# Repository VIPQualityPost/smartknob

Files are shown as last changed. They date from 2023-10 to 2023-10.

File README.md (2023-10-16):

# SmartKnob
SmartKnob is an open-source input device with software-configurable endstops and virtual detents.

A brushless gimbal motor is paired with a magnetic encoder to provide closed-loop torque feedback control, making it
possible to dynamically create and adjust the feel of detents and endstops.

Join the [Discord community](https://discord.gg/5jyhjcbTnR) to discuss the project with others, show off your build, or help answer each others' questions!




# Designs

## SmartKnob View
The "SmartKnob View" is the premium SmartKnob experience with an integrated display shown in my [demo video](https://www.youtube.com/watch?v=ip641WmY4pA). Under active development.

🎉 **Motors are [now available](https://www.sparkfun.com/products/20441)!** If you've been following this project,
you'll know that the recommended motors went out of stock nearly immediately after it was published.
Thanks to [the community](https://github.com/scottbez1/smartknob/issues/16#issuecomment-1094482805%5D), we were able to
identify the likely original manufacturer, and recently SparkFun Electronics has been getting them produced and regularly
[stocking them](https://www.sparkfun.com/products/20441)! (However, they've been selling out quickly each time they restock, so definitely sign up for backorder notifications if they're out of stock when you check). Thanks to everyone who helped search and investigate different
motor options along the way!

Features:
 - 240x240 round LCD ("GC9A01"), protected by 39.5mm watch glass on rotor
 - BLDC gimbal motor, with a hollow shaft for mechanically & electrically connecting the LCD
 - Powered by ESP32-PICO-V3-02 (Lilygo TMicro32 Plus module)
 - PCB flexure and SMD resistors used as strain gauges for press detection (haptic feedback provided via the motor)
 - 8 side-firing RGB LEDs (SK6812-SIDE-A) illuminate ring around the knob
 - USB-C (2.0) connector for 5V power and serial data/programming (CH340)
 - VEML7700 ambient light sensor for automatic backlight & LED intensity adjustment
 - Versatile back plate for mounting - use either 4x screws, or 2x 3M medium Command strips (with cutouts for accessing removal tabs after installation)
 - Front cover snaps on for easy access to the PCB

**Current status:** Not recommended for general use, but may be a fun project for an advanced electronics hobbyist.

### Demo video

<a href="https://www.youtube.com/watch?v=ip641WmY4pA">
    
</a>

### How it works
<a href="https://www.youtube.com/watch?v=Q76dMggUH1M">
    
</a>

### 3D CAD

Exploded view

Latest Fusion 360 Model: https://a360.co/3BzkU0n

### Build your own?

While this is a "DIY" open-source project, it is not yet a mature plug-and-play project. If you intend to build your own, note that it requires advanced soldering experience to build - very small-pitch surface-mount soldering is required (reflow or hot air recommended), and assembly is quite time-consuming and delicate. Please go into it with the expectation that you will almost certainly need to be able to troubleshoot some hardware and firmware issues yourself - I recommend reviewing/understanding the schematics and basic firmware before jumping in!

More documentation on the BOM and what parts you need to order is coming in the future - thanks so much for your interest! Follow me on [Twitter](https://twitter.com/scottbez1) for the latest updates on this and other projects.

View the latest auto-generated (untested) [Base PCB Interactive BOM](https://smartknob-artifacts.s3.us-west-1.amazonaws.com/master/electronics/view_base-ibom.html) and [Screen PCB Interactive BOM](https://smartknob-artifacts.s3.us-west-1.amazonaws.com/master/electronics/view_screen-ibom.html) (or, the combined [BOM csv](https://smartknob-artifacts.s3.us-west-1.amazonaws.com/master/electronics/view_base-bom.csv)) for electronics/hardware parts list. ⚠️ These are auto-generated from the latest untested revision on GitHub. For tested/stable/recommended artifacts, use a [release](https://github.com/scottbez1/smartknob/releases) instead.

A few miscellaneous notes in the meantime:

 - There's limited space inside the LCD mount for wiring, and 8 wires need to fit through the hole in the center. I used 30 AWG wire-wrapping wire. Enamel-coated wire would probably work too.
 - Older versions of the design (as seen in the videos) used glued-on BF350-3AA strain gauges to detect presses; in v0.5 these were replaced with footprints for SMD resistors, which exhibit similar properties when stretched/compressed and are much easier to assemble. 
 - The TMC6300 is _tiny_ and has a bottom pad, so I would seriously consider getting a stencil along with the PCB order. Even with the stencil I needed to manually clean up some bridging afterward; I _highly_ recommend Chip Quik NC191 gel flux, available on [Amazon](https://amzn.to/3MGDSr5) (or use this [non-affiliate link](https://www.amazon.com/Smooth-Flow-No-Clean-syringe-plunger/dp/B08KJPG3NZ) instead) or from your electronics distributor of choice. Flux is also very helpful when soldering the LCD ribbon cable to to screen PCB.
 - For breadboard prototyping, the [TMC6300-BOB](https://www.trinamic.com/support/eval-kits/details/tmc6300-bob/) or SparkFun's [TMC6300 driver board](https://www.sparkfun.com/products/21867) are awesome and way easier to work with than the bare chip if you just want to play around with low current BLDC motors
 - For AliExpress purchases: I highly recommend **only** using AliExpress Standard Shipping (purchasing in the US). I have had multiple purchases take months or never get delivered when purchased with Cainiao or other low cost shipping options, whereas AliExpress Standard is very reliable and generally faster in my experience.
 - Make sure to check the [open issues](https://github.com/scottbez1/smartknob/issues) - this design is not yet "stable", so beware that everything may not go smoothly.

Future plans:
 - consider switch to using an ESP32-S3-MINI-1 module
 - get wifi configured and working (probably MQTT?). Currently memory is an issue with the full display framebuffer sprite. PSRAM might fix this (requires newer ESP-IDF & unreleased Arduino core, and from a brief test I got horrible performance with PSRAM enabled), or the next item might help reduce memory:
 - migrate to LVGL, for better display rendering and easy support for menus, etc. Shouldn't require a full 240x240x24b framebuffer in memory, freeing some for wifi, etc.
 - Home Assistant integration, or other real-world applications
 - ???
 - [Profit](https://github.com/sponsors/scottbez1/) 😉

 #### Already built one?
Check out the [firmware/software documentation](https://paper.dropbox.com/doc/SmartKnob-firmware-and-software--B_oWj~L1dXqHgAqqYmhwwuqzAg-VUb9nq7btuhnHw5KlgJIH)
for tips on getting it programmed and hooking it up to your own software integrations.

If you've already uploaded the standard firmware and gone through the calibration process (see guide linked above if you don't know what this means),
go to https://scottbez1.github.io/smartknob/ to try out an interactive web-based demo that uses Web Serial to talk to a SmartKnob that's plugged into your
computer's USB port!

#### Base PCB

<a href="https://smartknob-artifacts.s3.us-west-1.amazonaws.com/master/electronics/view_base-front-3d.png">
    
</a>
<a href="https://smartknob-artifacts.s3.us-west-1.amazonaws.com/master/electronics/view_base-back-3d.png">
    
</a>

Ordering notes: use white soldermask, for reflecting light from RGB LED ring around the knob. Should be 1.2mm thick (not "standard" 1.6mm).

If you are ordering a stencil for solder paste from JLCPCB and plan to apply paste by hand (as
[shown in the video](https://youtu.be/Q76dMggUH1M?t=372)) without a stencil frame/machine, make sure to select
**"Customized size"** and enter smaller dimensions (e.g. 100mm x 100mm) to avoid getting a much larger stencil than you
need. This will also likely reduce the cost of shipping substantially! Also, select only the **Top** side; the bottom
only has 2 SMT components - the motor connector and VEML7700 ALS - so it's not worth getting a stencil for that.

Latest auto-generated (untested and likely broken!) artifacts⚠️:

[Schematic](https://smartknob-artifacts.s3.us-west-1.amazonaws.com/master/electronics/view_base-schematic.pdf)

[Interactive BOM](https://smartknob-artifacts.s3.us-west-1.amazonaws.com/master/electronics/view_base-ibom.html)

[PCB Packet](https://smartknob-artifacts.s3.us-west-1.amazonaws.com/master/electronics/view_base-pcb-packet.pdf)

[Gerbers](https://smartknob-artifacts.s3.us-west-1.amazonaws.com/master/electronics/view_base-jlc/gerbers.zip)

⚠️ For tested/stable/recommended artifacts, use a [release](https://github.com/scottbez1/smartknob/releases) instead.

#### Screen PCB

<a href="https://smartknob-artifacts.s3.us-west-1.amazonaws.com/master/electronics/view_screen-front-3d.png">
    
</a>
<a href="https://smartknob-artifacts.s3.us-west-1.amazonaws.com/master/electronics/view_screen-back-3d.png">
    
</a>

Ordering notes: Must be 1.2mm thick (not "standard" 1.6mm) per mechanical design. (The PCB silkscreen mentions 0.6mm thickness - this is the thickness of the **VHB tape** for adhering the LCD; the PCB should be 1.2mm thick)

There are few enough components on the Screen PCB that I chose to hand-solder them rather than reflow with solder paste
and a stencil, but if you order a stencil, see the note above about selecting a "Customized size" to be easier to
handle and save on shipping. Also make sure to select the **Bottom** side only; all the components are on the bottom
side of the screen PCB.

Latest auto-generated (untested and likely broken!) artifacts⚠️:

[Schematic](https://smartknob-artifacts.s3.us-west-1.amazonaws.com/master/electronics/view_screen-schematic.pdf)

[Interactive BOM](https://smartknob-artifacts.s3.us-west-1.amazonaws.com/master/electronics/view_screen-ibom.html)

[PCB Packet](https://smartknob-artifacts.s3.us-west-1.amazonaws.com/master/electronics/view_screen-pcb-packet.pdf)

[Gerbers](https://smartknob-artifacts.s3.us-west-1.amazonaws.com/master/electronics/view_screen-jlc/gerbers.zip)

⚠️ For tested/stable/recommended artifacts, use a [release](https://github.com/scottbez1/smartknob/releases) instead.

#### Printed parts
You will need six printed parts. The current stable designs can be found as STL assets in the [v185 mechanical release](https://github.com/scottbez1/smartknob/releases/tag/releases%2Fmechanical%2Fv185-dummy-tag) or you can export the latest untested designs from the CAD model by opening it in Fusion 360: https://a360.co/3BzkU0n

The parts can _probably_ be FDM 3D printed with a well-tuned printer, but the parts shown in videos/photos were MJF printed in nylon for tight tolerances and better surface finish. 

If you wanted a simpler build, you could omit the LCD and just merge the knob + glass from the model into a single STL to get a closed-top knob.

Export and print the following 6 parts:
* `Enclosure`
* `Knob` (RotorAssembly->KnobAssembly->Knob)
* `ScreenPlatform`
* `RotorSpacer` (RotorAssembly->RotorSpacer)
* `MountBase`
* `BackPlate`

⚠️ If you opt to go for MJF Nylon printing from JLCPCB, their system may complain about `< 0.8mm wall thickness detected` on the `MountBase`, `ScreenPlatform` and `RotorSpacer` parts. This appears to be a false positive, possibly on some of the print tapers. You should be able to ignore this, as all print orders at JLCPCB are subject to a final manual review, and they will contact you by email if there are any job-stopping issues or risks with your prints.

## NanoFOC (3rd party)
If you're looking to tinker with FOC/haptic feedback, but don't want to build a full SmartKnob View yourself, I can
recommend the NanoFOC DevKit++, an [open-source design](https://github.com/katbinaris/nanofoc_devkit) made and
[sold](https://store.binaris.io/products/nanofoc-devkit) by a member of the SmartKnob community! It's super compact
and is a great testbed or core for building your own BLDC-based haptic input device.

Image of the NanoFOC PCB

The NanoFOC uses an ESP32-S3, and the SmartKnob firmware works on it out of the box; just select the `nanofoc`
environment in PlatformIO rather than the `view` environment when uploading.

# Frequently Asked Questions (FAQ)

### Can I use this cheap gimbal BLDC motor I found on AliExpress?

I can't stop you, but I will caution that **you probably won't be super happy with it** depending on your intended application.

Nearly every off-the-shelf BLDC gimbal motor that the community has tested (which is pretty much ALL the cheap ones you'll find on AliExpress, trust me) has
_moderate to severge cogging_. That means the motor wants to snap to certain positions by itself even when unpowered. This means you won't be able to get
completely smooth rotation when virtual detents are turned off, and the motor's cogging may interfere with or overpower the virtual detents, particularly if
you set them to lower strength or make then very fine-grained.

The recommended motor is definitely the best (i.e. lowest cogging) off-the-shelf motor we've come across so far, and is the only readily-available motor
that I would consider "good" for this application.

If you've found another motor that is completely smooth when unpowered, we'd LOVE to hear about it in the discord; if you're wondering about some cheap motor
you saw online, either just order one and try it for yourself, or ask about it in discord but don't be surprised (or offended) if the response you get is
something terse like "nope, no good".

### How much does it cost?

I wish I could tell you now, but I don't actually know off the top of my head. Check back soon - I've only built a few so far, which was the result of a bunch of tinkering and prototyping over an extended period, so I don't have all the expenses tallied up yet. Probably less than $200 in parts? But some items have gotten more expensive, and you may be limited by minimum order quantities or shipping charges from multiple separate suppliers.

### Does it work with XYZ?

Not yet, regardless of whatever "XYZ" you're thinking of. So far I've only implemented enough firmware for the demo shown in the video, so you can't actually use it for anything productive yet. The basic detent configuration API is there, but not much else. Lots of firmware work remains to be done. If you build one, I'd love your help adding support for "XYZ" though!

### Can I buy one as a kit or already assembled?

Probably not? Or at least, I don't have any immediate plans to sell them myself. It's not that I don't want you to be happy, but hardware is a hard business and I just work on this stuff in my free time.

It's open source with a fairly permissive license though, so in theory anyone could start offering kits/assemblies. If someone does go down that route of selling them, note that attribution is
 _required_ (and I wouldn't say no to [royalties/tips/thanks](https://github.com/sponsors/scottbez1/) if you're in a giving mood 🙂).

# Firmware and Software
More extensive documentation of the firmware and software (and how to get started) can be found in the dedicated [SmartKnob Firmware and Software Guide](https://paper.dropbox.com/doc/SmartKnob-firmware-and-software--Byho6npe9XvZLZLxJ_8bK5TqAg-VUb9nq7btuhnHw5KlgJIH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)

## General Component Info

### Magnetic encoders

#### MT6701 (MagnTek)
Excellent sensor at a reasonable price - highly recommended. Less noisy than TLV493D, and more responsive (control loop is more stable) using SSI.

 - Lots of IO options - SSI, I2C, and ABZ - should offer good response latency
 - SSI includes CRC to validate data
 - No power-down or low-power options - may not be ideal for battery-powered devices
 - Not available from US distributors (Mouser, Digi-Key)

[Datasheet](http://www.magntek.com.cn/upload/MT6701_Rev.1.5.pdf)

[Ordering (LCSC)](https://lcsc.com/product-detail/Angle-Linear-Position-Sensors_Magn-Tek-MT6701CT-STD_C2856764.html)

#### TLV493D (Infineon)
Not used in the SmartKnob view, but a common/popular magnetic encoder in general. It's a mediocre choice for a haptic feedback implementation. Easy to prototype with using [Adafruit's QWIIC breakout board](https://www.adafruit.com/product/4366).

In my testing, it's noisy, requiring filtering/smoothing that can slow responsiveness, hurting control loop stability. Or, with less filtering, the noise
can easily be "amplified" by the derivative component in the PID motor torque controller, causing audible (and tactile) humming/buzzing.

But the bigger issue is that there is apparently a known silicon issue that causes the internal ADC to sometimes completely lock up, requiring a full reset and re-configuration, which can cause delays/gaps in data! See section
5.6 in the [User Manual](https://www.infineon.com/dgdl/Infineon-TLV493D-A1B6_3DMagnetic-UM-v01_03-EN.pdf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)

    In the Master Controlled Mode (MCM) or the Fast Mode (FM) the ADC conversion may hang up. A hang up can
    be detected by:
     - Frame Counter (FRM) counter stucks and does not increment anymore.

In my experience testing 4 different Adafruit breakout boards, 2 of them (50%) regularly exhibit this lockup behavior within a minute or two of use. It is possible to detect and auto-reset (and there is code in the project to do so), but it is slow and may cause undesirable jumps/delays if the sensor locks up often.

[Datasheet](https://www.mouser.com/datasheet/2/196/Infineon_TLV493D_A1B6_DataSheet_v01_10_EN-1227967.pdf)

#### AS5600 (AMS)
A mediocre choice. Cheap breakout boards are readily available.

In my testing, it's fairly noisy (anecdotally, noisier than the TLV493d), requiring filtering/smoothing that can slow responsiveness, hurting control loop stability. Additionally, it saturates at a lower magnetic field strength than other sensors I tested, requiring a significant air gap (8-10mm) when used with a strong neodymium diametric magnet like [Radial Magnets 8995](https://www.digikey.com/en/products/detail/radial-magnets-inc/8995/5126077).

[Datasheet](https://ams.com/documents/20143/36005/AS5600_DS000365_5-00.pdf)

### Motor drivers
#### TMC6300-LA
This is a relatively new IC and it's a perfect match! There generally aren't any other drivers (with integrated fets) that meet the requirements for the low-voltage and low-current motors used in this project (DRV8316 might work, but has not been tested).

Highlights:
 - 2-11V DC motor supply input
 - Up to 1.2A RMS
 - Tiny (3x3mm QFN)

 [Datasheet](https://www.trinamic.com/fileadmin/assets/Products/ICs_Documents/TMC6300_datasheet_rev1.07.pdf)

 [Product page](https://www.trinamic.com/products/integrated-circuits/details/tmc6300-la/)

### Motors
#### 32mm Rotor, Hollow Shaft, Diametric magnet



- 32mm rotor
- 15mm overall height (including magnet), 12.75mm height w/o magnet, 9mm rotor height
- low/zero cogging - excellent for completely smooth input
- 5.9mm hollow shaft
- built-in diametric magnet for encoder
- Proven option

This is overall the easiest motor to get started with. Low cogging and a built-in diametric magnet are great!

Available [from SparkFun](https://www.sparkfun.com/products/20441)!

# Acknowledgements
This project was greatly inspired by Jesse Schoch's video "[haptic textures and virtual detents](https://www.youtube.com/watch?v=1gPQfDkX3BU)" and the
corresponding [discussion in the SimpleFOC community](https://community.simplefoc.com/t/haptic-textures/301). Seriously, this project wouldn't exist if not for that video - thank you Jesse!

# License

This project is licensed under Apache v2 (software, electronics, documentation) and Creative Commons Attribution 4.0 (hardware/mechanical) (see [LICENSE.txt](LICENSE.txt) and [Creative Commons](https://creativecommons.org/licenses/by/4.0/)).

    Copyright 2022 Scott Bezek
    
    Licensed under the Apache License, Version 2.0 (the "License");
    you may not use this file except in compliance with the License.
    You may obtain a copy of the License at
    
        http://www.apache.org/licenses/LICENSE-2.0
    
    Unless required by applicable law or agreed to in writing, software
    distributed under the License is distributed on an "AS IS" BASIS,
    WITHOUT WARRANTIES OR CONDITIONS OF ANY KIND, either express or implied.
    See the License for the specific language governing permissions and
    limitations under the License.

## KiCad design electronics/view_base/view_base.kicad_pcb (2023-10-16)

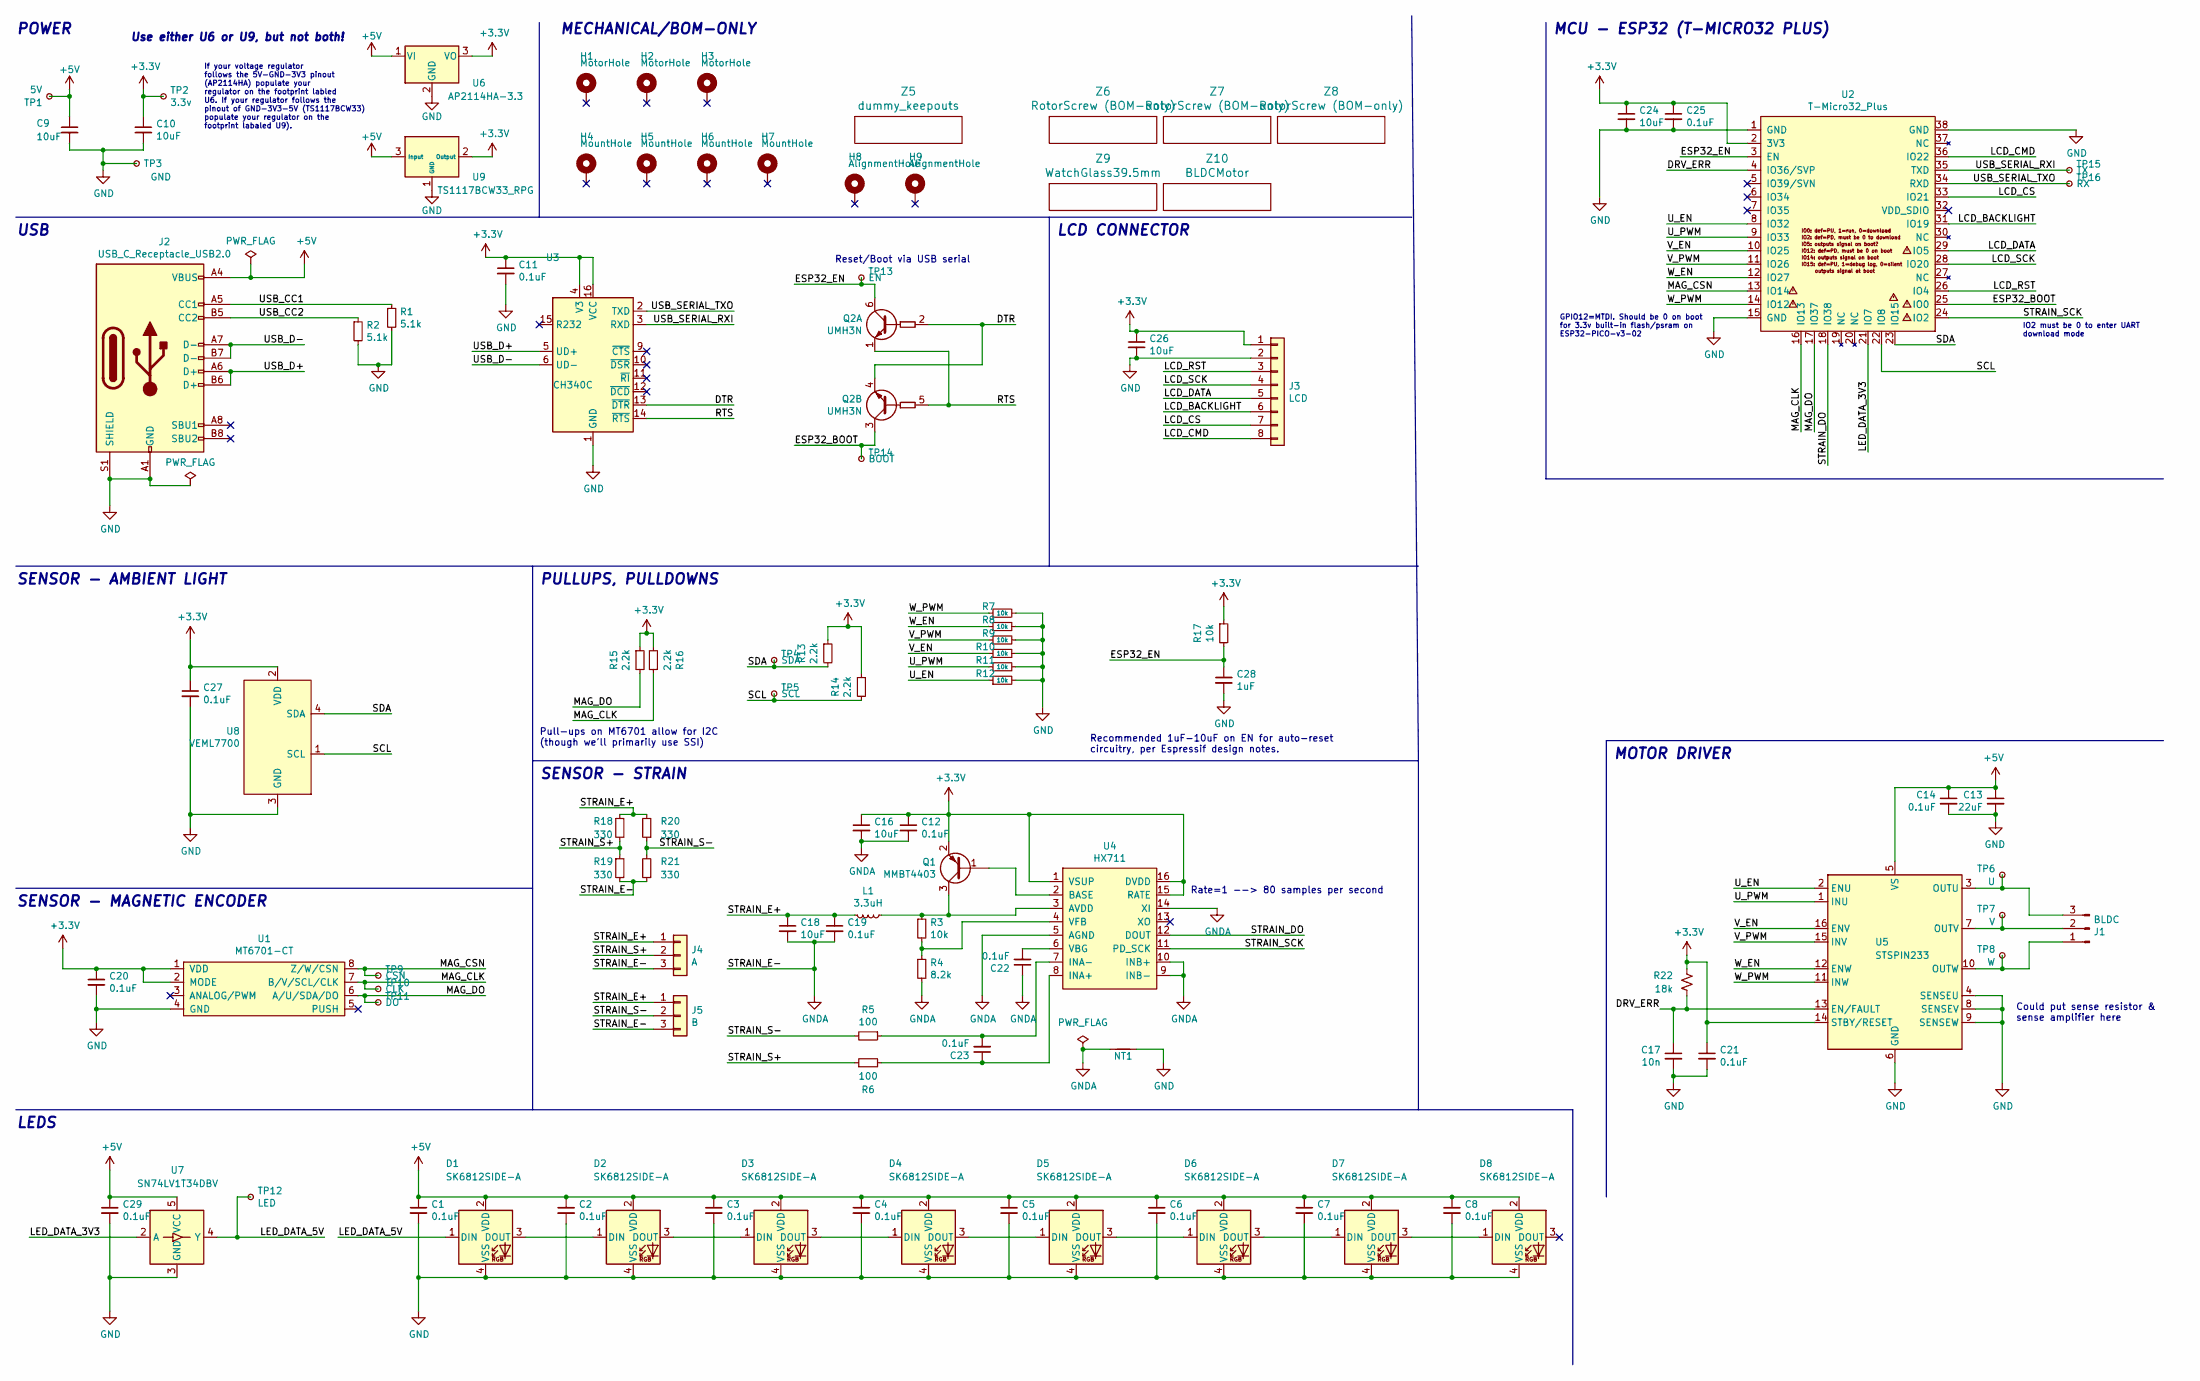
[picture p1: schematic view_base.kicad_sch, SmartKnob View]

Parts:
C1, C2, C3, C4, C5, C6, C7, C8, C11, C12, C14, C19, C20, C21, C22, C23, C25, C27, C29: 0.1uF; C_0603_1608Metric; LCSC C1591
C9, C10, C16, C18, C24, C26: 10uF; C_0805_2012Metric; LCSC C2922480
C13: 22uF; C_0805_2012Metric; LCSC C98190
C17: 10n; C_0603_1608Metric; LCSC C1591
C28: 1uF; C_0603_1608Metric; Mouser 187-CL10A105KA8NNNC
D1, D2, D3, D4, D5, D6, D7, D8: SK6812SIDE-A; SK6812-SIDE-A; Digikey 1528-4691-ND
H1, H2, H3: MotorHole; MountingHole_M1.6; LCSC C2931389
H4, H5, H6, H7: MountHole; MountingHole_2.2mm_M2_ISO7380_Pad_NonVirtual; LCSC C2911210 or C2911532 (screw), C2961595 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
H8, H9: AlignmentHole; MountingHole_2.2mm_M2_ISO7380_Pad_NonVirtual
J1: BLDC; 532610371; LCSC C293630
J2: USB_C_Receptacle_USB2.0; USB4510_NoPaste; LCSC C428463
J3: LCD; SolderPads_2mm_8
J4: A; SolderPads_2mm_3_STRAIN
J5: B; SolderPads_2mm_3_STRAIN
L1: 3.3uH; L_0805_2012Metric; LCSC C307744
NT1: NetTie_2; NetTie-2_SMD_Pad0.5mm
Q1: MMBT4403; SOT-23; LCSC C78864
Q2: UMH3N; SOT-363_SC-70-6; LCSC C62892
R1, R2: 5.1k; R_0603_1608Metric; LCSC C105580
R3, R7, R8, R9, R10, R11, R12, R17: 10k; R_0603_1608Metric; LCSC C98220
R4: 8.2k; R_0603_1608Metric; LCSC C114637
R5, R6: 100; R_0603_1608Metric; LCSC C319953
R13, R14, R15, R16: 2.2k; R_0603_1608Metric; LCSC C4190
R18, R19, R20, R21: 330; R_2512_6332Metric; LCSC C19866
R22: 18k; R_0603_1608Metric
TP1: 5V; TestPoint_Pad_D2.0mm_ValueSilk
TP2: 3.3v; TestPoint_Pad_D2.0mm_ValueSilk
TP3: GND; TestPoint_Pad_D2.0mm_ValueSilk
TP4: SDA; TestPoint_Pad_D2.0mm_ValueSilk
TP5: SCL; TestPoint_Pad_D2.0mm_ValueSilk
TP6: U; TestPoint_Pad_D2.0mm_ValueSilk
TP7: V; TestPoint_Pad_D2.0mm_ValueSilk
TP8: W; TestPoint_Pad_D2.0mm_ValueSilk
TP9: CSN; TestPoint_Pad_D2.0mm_ValueSilk
TP10: CLK; TestPoint_Pad_D2.0mm_ValueSilk
TP11: DO; TestPoint_Pad_D2.0mm_ValueSilk
TP12: LED; TestPoint_Pad_D2.0mm_ValueSilk
TP13: EN; TestPoint_Pad_D2.0mm_ValueSilk
TP14: BOOT; TestPoint_Pad_D2.0mm_ValueSilk
TP15: TX; TestPoint_Pad_D2.0mm_ValueSilk
TP16: RX; TestPoint_Pad_D2.0mm_ValueSilk
U1: MT6701-CT; SOIC-8_3.9x4.9mm_P1.27mm; LCSC C2856764, or C3003196
U2: T-Micro32_Plus; T-Micro32; Digikey N/A
U3: CH340C; SOIC-16_3.9x9.9mm_P1.27mm; LCSC C84681
U4: HX711; SOIC-16_3.9x9.9mm_P1.27mm; LCSC C43656
U5: STSPIN233; VQFN-16-1EP_3x3mm_P0.5mm_EP1.8x1.8mm
U6: AP2114HA-3.3; SOT-223-3_TabPin2_InGndOut; LCSC C460314
U7: SN74LV1T34DBV; SOT-23-5; LCSC C100024
U8: VEML7700; VEML7700-TOP; Digikey VEML7700-TT
U9: TS1117BCW33_RPG; SOT-223-3_TabPin2_GndOutIn; LCSC C6186, C35879, or others
Z5: dummy_keepouts; ViewKeepouts3d
Z6, Z7, Z8: RotorScrew (BOM-only); bom_only_no_pin
Z9: WatchGlass39.5mm; bom_only_no_pin
Z10: BLDCMotor; bom_only_no_pin

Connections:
+3V3: C10.1, C11.1, C12.1, C16.1, C20.1, C21.1, C24.1, C25.1, C26.1, C27.1, J3.1, Q1.2 (E), R13.1, R14.1, R15.1, R16.2, R17.1, R22.1, TP2.1, U1.1 (VDD), U1.2 (MODE), U2.2 (3V3), U3.4 (V3), U3.16 (VCC), U4.1 (VSUP), U4.15 (RATE), U4.16 (DVDD), U5.14 (STBY/RESET), U6.3 (VO), U8.2 (VDD), U9.2 (Output)
+5V: C1.1, C2.1, C3.1, C4.1, C5.1, C6.1, C7.1, C8.1, C9.1, C13.1, C14.1, C29.1, D1.2 (VDD), D2.2 (VDD), D3.2 (VDD), D4.2 (VDD), D5.2 (VDD), D6.2 (VDD), D7.2 (VDD), D8.2 (VDD), J2.A4 (VBUS), J2.A9 (VBUS), J2.B4 (VBUS), J2.B9 (VBUS), TP1.1, U5.5 (VS), U6.1 (VI), U7.5 (VCC), U9.3 (Input)
/DRV_ERR: C17.1, R22.2, U2.4 (IO36/SVP), U5.13 (EN/FAULT)
/DTR: Q2.2 (B1), Q2.4 (E2), U3.13 (~DTR)
/ESP32_BOOT: Q2.3 (C2), TP14.1, U2.25 (IO0)
/ESP32_EN: C28.1, Q2.6 (C1), R17.2, TP13.1, U2.3 (EN)
/LCD_BACKLIGHT: J3.6, U2.31 (IO19)
/LCD_CMD: J3.8, U2.36 (IO22)
/LCD_CS: J3.7, U2.33 (IO21)
/LCD_DATA: J3.5, U2.29 (IO5)
/LCD_RST: J3.3, U2.26 (IO4)
/LCD_SCK: J3.4, U2.28 (IO20)
/LED_DATA_3V3: U2.21 (IO7), U7.2 (A)
/LED_DATA_5V: D1.1 (DIN), TP12.1, U7.4 (Y)
/MAG_CLK: R16.1, TP10.1, U1.7 (B/V/SCL/CLK), U2.16 (IO13)
/MAG_CSN: TP9.1, U1.8 (Z/W/CSN), U2.13 (IO14)
/MAG_DO: R15.2, TP11.1, U1.6 (A/U/SDA/DO), U2.17 (IO37)
/RTS: Q2.1 (E1), Q2.5 (B2), U3.14 (~RTS)
/SCL: R14.2, TP5.1, U2.22 (IO8), U8.1 (SCL)
/SDA: R13.2, TP4.1, U2.23 (IO15), U8.4 (SDA)
/STRAIN_DO: U2.18 (IO38), U4.12 (DOUT)
/STRAIN_E+: C18.1, C19.1, J4.1, J5.1, L1.2, R18.1, R20.2
/STRAIN_S+: J4.2, R6.1, R18.2, R19.1
/STRAIN_S-: J5.2, R5.2, R20.1, R21.2
/STRAIN_SCK: U2.24 (IO2), U4.11 (PD_SCK)
/USB_CC1: J2.A5 (CC1), R1.1
/USB_CC2: J2.B5 (CC2), R2.1
/USB_D+: J2.A6 (D+), J2.B6 (D+), U3.5 (UD+)
/USB_D-: J2.A7 (D-), J2.B7 (D-), U3.6 (UD-)
/USB_SERIAL_RXI: TP15.1, U2.35 (TXD), U3.3 (RXD)
/USB_SERIAL_TXO: TP16.1, U2.34 (RXD), U3.2 (TXD)
/U_EN: R12.1, U2.8 (IO32), U5.2 (ENU)
/U_PWM: R11.1, U2.9 (IO33), U5.1 (INU)
/V_EN: R10.1, U2.10 (IO25), U5.16 (ENV)
/V_PWM: R9.1, U2.11 (IO26), U5.15 (INV)
/W_EN: R8.1, U2.12 (IO27), U5.12 (ENW)
/W_PWM: R7.1, U2.14 (IO12), U5.11 (INW)
GND: C1.2, C2.2, C3.2, C4.2, C5.2, C6.2, C7.2, C8.2, C9.2, C10.2, C11.2, C13.2, C14.2, C17.2, C20.2, C21.2, C24.2, C25.2, C26.2, C27.2, C28.2, C29.2, D1.4 (VSS), D2.4 (VSS), D3.4 (VSS), D4.4 (VSS), D5.4 (VSS), D6.4 (VSS), D7.4 (VSS), D8.4 (VSS), J2.A1 (GND), J2.A12 (GND), J2.B1 (GND), J2.B12 (GND), J2.S1 (SHIELD), J3.2, NT1.2, R1.2, R2.2, R7.2, R8.2, R9.2, R10.2, R11.2, R12.2, TP3.1, U1.4 (GND), U2.1 (GND), U2.15 (GND), U2.38 (GND), U3.1 (GND), U5.4 (SENSEU), U5.6 (GND), U5.8 (SENSEV), U5.9 (SENSEW), U5.17 (GND), U6.2 (GND), U7.3 (GND), U8.3 (GND), U9.1 (GND)
GNDA: C12.2, C16.2, C18.2, C19.2, C22.1, J4.3, J5.3, NT1.1, R4.2, R19.2, R21.1, U4.5 (AGND), U4.9 (INB-), U4.10 (INB+), U4.14 (XI)
unnamed: D1.3 (DOUT), D2.1 (DIN)
unnamed: D2.3 (DOUT), D3.1 (DIN)
unnamed: D3.3 (DOUT), D4.1 (DIN)
unnamed: D4.3 (DOUT), D5.1 (DIN)
unnamed: D5.3 (DOUT), D6.1 (DIN)
unnamed: D6.3 (DOUT), D7.1 (DIN)
unnamed: D7.3 (DOUT), D8.1 (DIN)
unnamed: J1.1, TP8.1, U5.10 (OUTW)
unnamed: J1.2, TP7.1, U5.7 (OUTV)
unnamed: J1.3, TP6.1, U5.3 (OUTU)
unnamed: Q1.1 (B), U4.2 (BASE)
unnamed: L1.1, Q1.3 (C), R3.1, U4.3 (AVDD)
unnamed: C23.1, R6.2, U4.8 (INA+)
unnamed: C23.2, R5.1, U4.7 (INA-)
unnamed: C22.2, U4.6 (VBG)
unnamed: R3.2, R4.1, U4.4 (VFB)

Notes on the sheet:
POWER
Could put sense resistor & sense amplifier here
MCU - ESP32 (T-MICRO32 PLUS)
If your voltage regulator follows the 5V-GND-3V3 pinout (AP2114HA) populate your regulator on the footprint labled U6. If your regulator follows the pinout of GND-3V3-5V (TS1117BCW33) populate your regulator on the footprint labaled U9).
SENSOR - MAGNETIC ENCODER
MOTOR DRIVER
MECHANICAL/BOM-ONLY
IO2 must be 0 to enter UART download mode
GPIO12=MTDI. Should be 0 on boot for 3.3v built-in flash/psram on ESP32-PICO-v3-02
Pull-ups on MT6701 allow for I2C (though we'll primarily use SSI)
Use either U6 or U9, but not both!
Rate=1 --> 80 samples per second
SENSOR - AMBIENT LIGHT
Recommended 1uF-10uF on EN for auto-reset circuitry, per Espressif design notes.
USB
SENSOR - STRAIN
LEDS
PULLUPS, PULLDOWNS
LCD CONNECTOR
Reset/Boot via USB serial

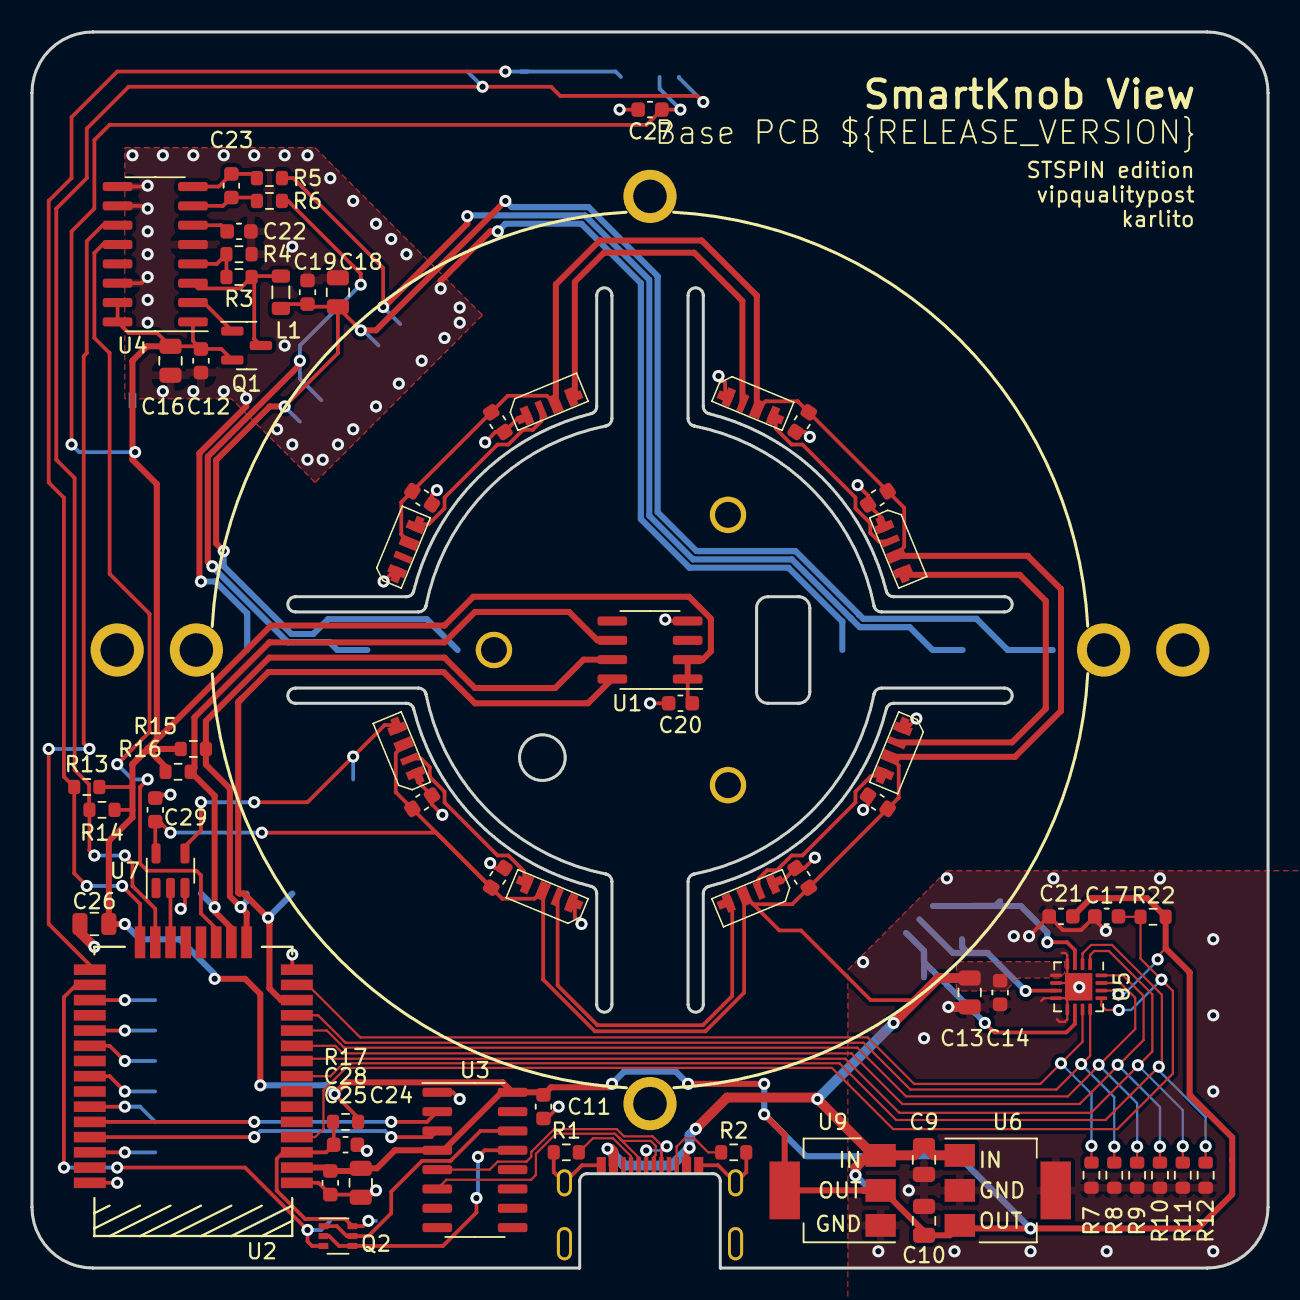
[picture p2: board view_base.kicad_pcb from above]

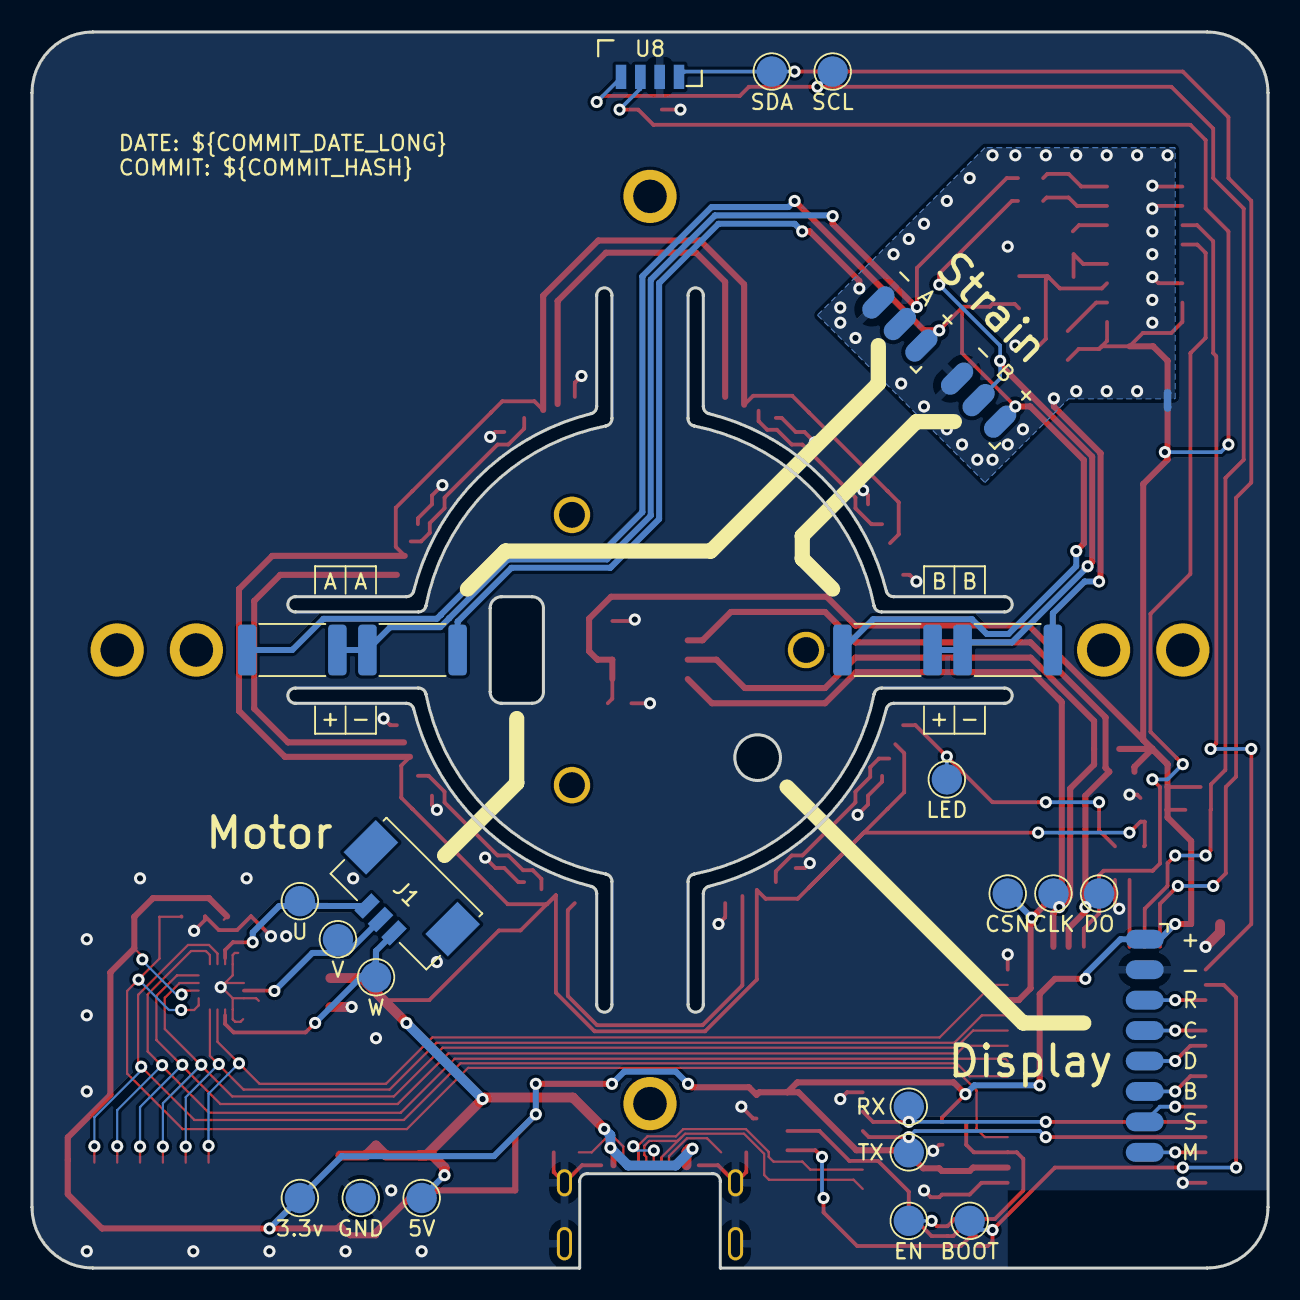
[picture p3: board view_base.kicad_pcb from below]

Board: 2 copper layers, 81.2 x 81.2 mm, 107 parts (26 on the bottom side), 55 nets.

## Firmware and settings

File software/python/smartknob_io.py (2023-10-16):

if __name__ == '__main__':
    import sys
    sys.exit('This is a library file to be imported into your own python scripts. It doesn\'t do anything if run directly')


from cobs import cobs
from collections import (
    defaultdict,
)
from contextlib import contextmanager
from enum import Enum
import logging
import os
from queue import (
    Empty,
    Full,
    Queue,
)
from random import randint
import serial
import serial.tools.list_ports
import sys
from threading import (
    Thread,
    Lock,
)
import time
import zlib

software_root = os.path.dirname(os.path.abspath(__file__))
sys.path.append(os.path.join(software_root, 'proto_gen'))

from proto_gen import smartknob_pb2

SMARTKNOB_BAUD = 921600
PROTOBUF_PROTOCOL_VERSION = 1


class Smartknob(object):
    RETRY_TIMEOUT = 0.25

    def __init__(self, serial_instance):
        self._serial = serial_instance
        self._logger = logging.getLogger('smartknob')
        self._out_q = Queue()
        self._ack_q = Queue()
        self._next_nonce = randint(0, 255)
        self._run = True

        self._lock = Lock()
        self._message_handlers = defaultdict(list)

    def _read_loop(self):
        self._logger.debug('Read loop started')
        buffer = b''
        while True:
            buffer += self._serial.read_until(b'\0')
            if not self._run:
                return

            if not len(buffer):
                continue

            if not buffer.endswith(b'\0'):
                continue
            
            self._process_frame(buffer[:-1])
            buffer = b''

    def _process_frame(self, frame):
        try:
            decoded = cobs.decode(frame)
        except cobs.DecodeError:
            self._logger.debug(f'Failed decode ({len(frame)} bytes)')
            self._logger.debug(frame)
            return

        if len(decoded) < 4:
            return

        payload = decoded[:-4]
        expected_crc = zlib.crc32(payload) & 0xffffffff
        provided_crc = (decoded[-1] << 24) \
                        | (decoded[-2] << 16) \
                        | (decoded[-3] << 8) \
                        | decoded[-4]
        
        if expected_crc != provided_crc:
            self._logger.debug(f'Bad CRC. expected={hex(expected_crc)}, actual={hex(provided_crc)}')
            return

        message = smartknob_pb2.FromSmartKnob()
        message.ParseFromString(payload)
        self._logger.debug(message)
        if message.protocol_version != PROTOBUF_PROTOCOL_VERSION:
            self._logger.warn(f'Invalid protocol version. Expected {PROTOBUF_PROTOCOL_VERSION}, received {message.protocol_version}')

        payload_type = message.WhichOneof('payload')

        # If this is an ack, notify the write thread
        if payload_type == 'ack':
            nonce = message.ack.nonce
            self._ack_q.put(nonce)

        with self._lock:
            for handler in self._message_handlers[payload_type] + self._message_handlers[None]:
                try:
                    handler(getattr(message, payload_type))
                except:
                    self._logger.warning(f'Unhandled exception in message handler ({payload_type})', exc_info=True)
    
    def _write_loop(self):
        self._logger.debug('Write loop started')
        while True:
            data = self._out_q.get()
            # Check for shutdown
            if not self._run:
                self._logger.debug('Write loop exiting @ _out_q')
                return
            (nonce, encoded_message) = data

            next_retry = 0
            while True:
                if time.time() >= next_retry:
                    if next_retry > 0:
                        self._logger.debug('Retry write...')
                    self._serial.write(encoded_message)
                    self._serial.write(b'\0')
                    next_retry = time.time() + Smartknob.RETRY_TIMEOUT
                
                try:
                    latest_ack_nonce = self._ack_q.get(timeout=next_retry - time.time())
                except Empty:
                    latest_ack_nonce = None

                # Check for shutdown
                if not self._run:
                    self._logger.debug('Write loop exiting @ _ack_q')
                    return

                if latest_ack_nonce == nonce:
                    break
                else:
                    self._logger.debug(f'Got unexpected nonce: {latest_ack_nonce}')
    
    def _enqueue_message(self, message):
        nonce = self._next_nonce
        self._next_nonce += 1

        message.protocol_version = PROTOBUF_PROTOCOL_VERSION
        message.nonce = nonce

        payload = bytearray(message.SerializeToString())

        crc = zlib.crc32(payload) & 0xffffffff
        payload.append(crc & 0xff)
        payload.append((crc >> 8) & 0xff)
        payload.append((crc >> 16) & 0xff)
        payload.append((crc >> 24) & 0xff)

        encoded_message = cobs.encode(payload)

        self._out_q.put((nonce, encoded_message))

        approx_q_length = self._out_q.qsize()
        self._logger.debug(f'Out q length: {approx_q_length}')
        if approx_q_length > 10:
            self._logger.warning(f'Output queue length is high! ({approx_q_length}) Is the smartknob still connected and functional?')

    def set_config(self, config):
        message = smartknob_pb2.ToSmartknob()
        message.smartknob_config.CopyFrom(config)
        self._enqueue_message(message)

    def start(self):
        self.read_thread = Thread(target=self._read_loop)
        self.write_thread = Thread(target=self._write_loop)
        self.read_thread.start()
        self.write_thread.start()
    
    def shutdown(self):
        self._logger.info('Shutting down...')
        self._run = False
        self.read_thread.join()
        self._logger.debug('Read thread terminated')
        self._out_q.put(None)
        self._ack_q.put(None)
        self.write_thread.join()
        self._logger.debug('Write thread terminated')
    
    def add_handler(self, message_type, handler):
        with self._lock:
            self._message_handlers[message_type].append(handler)
        return lambda: self._remove_handler(message_type, handler)

    def _remove_handler(self, message_type, handler):
        with self._lock:
            self._message_handlers[message_type].remove(handler)

    def request_state(self):
        message = smartknob_pb2.ToSmartknob()
        message.request_state.SetInParent()
        self._enqueue_message(message)

    def hard_reset(self):
        self._serial.setRTS(True)
        self._serial.setDTR(False)
        time.sleep(0.2)
        self._serial.setDTR(True)
        time.sleep(0.2)


@contextmanager
def smartknob_context(serial_port, default_logging=True, wait_for_comms=True):
    with serial.Serial(serial_port, SMARTKNOB_BAUD, timeout=1.0) as ser:
        s = Smartknob(ser)
        s.start()

        if default_logging:
            s.add_handler('log', lambda msg: s._logger.info(f'From smartknob: {msg.msg}'))

        if wait_for_comms:
            s._logger.info('Connecting to smartknob...')
            q = Queue(1)
            def startup_handler(message):
                try:
                    q.put_nowait(None)
                except Full:
                    pass
            unregister = s.add_handler('smartknob_state', startup_handler)

            s.request_state()
            q.get()
            unregister()
            s._logger.info('Connected!')

        try:
            yield s
        finally:
            s.shutdown()


def ask_for_serial_port():
    """
    Helper function to ask which port to use via stdin
    """
    print('Available ports:')
    ports = sorted(
        filter(
            lambda p: p.description != 'n/a',
            serial.tools.list_ports.comports(),
        ),
        key=lambda p: p.device,
    )
    for i, port in enumerate(ports):
        print('[{: 2}] {} - {}'.format(i, port.device, port.description))
    print()
    value = input('Use which port? ')
    port_index = int(value)
    assert 0 <= port_index < len(ports)
    return ports[port_index].device

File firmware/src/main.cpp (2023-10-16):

#include <Arduino.h>

#include "configuration.h"
#include "display_task.h"
#include "interface_task.h"
#include "motor_task.h"

Configuration config;

#if SK_DISPLAY
static DisplayTask display_task(0);
static DisplayTask* display_task_p = &display_task;
#else
static DisplayTask* display_task_p = nullptr;
#endif
static MotorTask motor_task(1, config);


InterfaceTask interface_task(0, motor_task, display_task_p);

void setup() {
  #if SK_DISPLAY
  display_task.setLogger(&interface_task);
  display_task.begin();

  // Connect display to motor_task's knob state feed
  motor_task.addListener(display_task.getKnobStateQueue());
  #endif

  interface_task.begin();

  config.setLogger(&interface_task);
  config.loadFromDisk();

  interface_task.setConfiguration(&config);

  motor_task.setLogger(&interface_task);
  motor_task.begin();

  // Free up the Arduino loop task
  vTaskDelete(NULL);
}

void loop() {
  // char buf[50];
  // static uint32_t last_stack_debug;
  // if (millis() - last_stack_debug > 1000) {
  //   interface_task.log("Stack high water:");
  //   snprintf(buf, sizeof(buf), "  main: %d", uxTaskGetStackHighWaterMark(NULL));
  //   interface_task.log(buf);
  //   #if SK_DISPLAY
  //     snprintf(buf, sizeof(buf), "  display: %d", uxTaskGetStackHighWaterMark(display_task.getHandle()));
  //     interface_task.log(buf);
  //   #endif
  //   snprintf(buf, sizeof(buf), "  motor: %d", uxTaskGetStackHighWaterMark(motor_task.getHandle()));
  //   interface_task.log(buf);
  //   snprintf(buf, sizeof(buf), "  interface: %d", uxTaskGetStackHighWaterMark(interface_task.getHandle()));
  //   interface_task.log(buf);
  //   snprintf(buf, sizeof(buf), "Heap -- free: %d, largest: %d", heap_caps_get_free_size(MALLOC_CAP_8BIT), heap_caps_get_largest_free_block(MALLOC_CAP_8BIT));
  //   interface_task.log(buf);
  //   last_stack_debug = millis();
  // }
}

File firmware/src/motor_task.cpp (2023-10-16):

#include <SimpleFOC.h>

#include "motor_task.h"
#if SENSOR_MT6701
#include "mt6701_sensor.h"
#elif SENSOR_TLV
#include "tlv_sensor.h"
#elif SENSOR_MAQ430
#include "maq430_sensor.h"
#endif

#include "motors/motor_config.h"
#include "util.h"

static const float DEAD_ZONE_DETENT_PERCENT = 0.2;
static const float DEAD_ZONE_RAD = 1 * _PI / 180;

static const float IDLE_VELOCITY_EWMA_ALPHA = 0.001;
static const float IDLE_VELOCITY_RAD_PER_SEC = 0.05;
static const uint32_t IDLE_CORRECTION_DELAY_MILLIS = 500;
static const float IDLE_CORRECTION_MAX_ANGLE_RAD = 5 * PI / 180;
static const float IDLE_CORRECTION_RATE_ALPHA = 0.0005;


MotorTask::MotorTask(const uint8_t task_core, Configuration& configuration) : Task("Motor", 4000, 1, task_core), configuration_(configuration) {
    queue_ = xQueueCreate(5, sizeof(Command));
    assert(queue_ != NULL);
}

MotorTask::~MotorTask() {}


#if SENSOR_TLV
    TlvSensor encoder = TlvSensor();
#elif SENSOR_MT6701
    MT6701Sensor encoder = MT6701Sensor();
#elif SENSOR_MAQ430
    MagneticSensorSPI encoder = MagneticSensorSPI(MAQ430_SPI, PIN_MAQ_SS);
#endif

void MotorTask::run() {

    driver.voltage_power_supply = 5;
    driver.init();

    #if SENSOR_TLV
    encoder.init(&Wire, false);
    #elif SENSOR_MT6701
    encoder.init();
    #elif SENSOR_MAQ430
    SPIClass* spi = new SPIClass(HSPI);
    spi->begin(PIN_MAQ_SCK, PIN_MAQ_MISO, PIN_MAQ_MOSI, PIN_MAQ_SS);
    encoder.init(spi);
    #endif

    motor.linkDriver(&driver);

    motor.controller = MotionControlType::torque;
    motor.voltage_limit = FOC_VOLTAGE_LIMIT;
    motor.velocity_limit = 10000;
    motor.linkSensor(&encoder);

    // Not actually using the velocity loop built into SimpleFOC; but I'm using those PID variables
    // to run PID for torque (and SimpleFOC studio supports updating them easily over serial for tuning)
    motor.PID_velocity.P = FOC_PID_P;
    motor.PID_velocity.I = FOC_PID_I;
    motor.PID_velocity.D = FOC_PID_D;
    motor.PID_velocity.output_ramp = FOC_PID_OUTPUT_RAMP;
    motor.PID_velocity.limit = FOC_PID_LIMIT;

    #ifdef FOC_LPF
    motor.LPF_angle.Tf = FOC_LPF;
    #endif

    motor.init();

    encoder.update();
    delay(10);

    PB_PersistentConfiguration c = configuration_.get();
    motor.pole_pairs = c.motor.calibrated ? c.motor.pole_pairs : 7;
    motor.initFOC(c.motor.zero_electrical_offset, c.motor.direction_cw ? Direction::CW : Direction::CCW);

    motor.monitor_downsample = 0; // disable monitor at first - optional

    // disableCore0WDT();

    float current_detent_center = motor.shaft_angle;
    PB_SmartKnobConfig config = {
        .position = 0,
        .sub_position_unit = 0,
        .position_nonce = 0,
        .min_position = 0,
        .max_position = 1,
        .position_width_radians = 60 * _PI / 180,
        .detent_strength_unit = 0,
    };
    int32_t current_position = 0;
    float latest_sub_position_unit = 0;

    float idle_check_velocity_ewma = 0;
    uint32_t last_idle_start = 0;
    uint32_t last_publish = 0;

    while (1) {
        motor.loopFOC();

        // Check queue for pending requests from other tasks
        Command command;
        if (xQueueReceive(queue_, &command, 0) == pdTRUE) {
            switch (command.command_type) {
                case CommandType::CALIBRATE:
                    calibrate();
                    break;
                case CommandType::CONFIG: {
                    // Check new config for validity
                    PB_SmartKnobConfig& new_config = command.data.config;
                    if (new_config.detent_strength_unit < 0) {
                        log("Ignoring invalid config: detent_strength_unit cannot be negative");
                        break;
                    }
                    if (new_config.endstop_strength_unit < 0) {
                        log("Ignoring invalid config: endstop_strength_unit cannot be negative");
                        break;
                    }
                    if (new_config.snap_point < 0.5) {
                        log("Ignoring invalid config: snap_point must be >= 0.5 for stability");
                        break;
                    }
                    if (new_config.detent_positions_count > COUNT_OF(new_config.detent_positions)) {
                        log("Ignoring invalid config: detent_positions_count is too large");
                        break;
                    }
                    if (new_config.snap_point_bias < 0) {
                        log("Ignoring invalid config: snap_point_bias cannot be negative or there is risk of instability");
                        break;
                    }

                    // Change haptic input mode
                    bool position_updated = false;
                    if (new_config.position != config.position
                            || new_config.sub_position_unit != config.sub_position_unit
                            || new_config.position_nonce != config.position_nonce) {
                        log("applying position change");
                        current_position = new_config.position;
                        position_updated = true;
                    }

                    if (new_config.min_position <= new_config.max_position) {
                        // Only check bounds if min/max indicate bounds are active (min >= max)
                        if (current_position < new_config.min_position) {
                            current_position = new_config.min_position;
                            log("adjusting position to min");
                        } else if (current_position > new_config.max_position) {
                            current_position = new_config.max_position;
                            log("adjusting position to max");
                        }
                    }

                    if (position_updated || new_config.position_width_radians != config.position_width_radians) {
                        log("adjusting detent center");
                        float new_sub_position = position_updated ? new_config.sub_position_unit : latest_sub_position_unit;
                        #if SK_INVERT_ROTATION
                            float shaft_angle = -motor.shaft_angle;
                        #else
                            float shaft_angle = motor.shaft_angle;
                        #endif
                        current_detent_center = shaft_angle + new_sub_position * new_config.position_width_radians;
                    }
                    config = new_config;
                    log("Got new config");
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

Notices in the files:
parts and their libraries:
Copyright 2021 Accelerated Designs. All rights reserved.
